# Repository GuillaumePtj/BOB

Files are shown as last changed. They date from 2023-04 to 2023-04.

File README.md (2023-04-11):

# BOB

This project is carried out by a for students group in second year at ENSEA.

### Principal objectives

This project main goal is to realize a 5-axis robot arm. This robot is a prototype concive to help people with disabilities. 

### Requirement

This project is realized in collaboration with a clinique, and some decision were taken.
The robot need :

  * to draw its power supply from the grid
  * to be able to pick up something from the floor where he stand
  * to be connected at the wheelchair of the patient in bluetooth
  * to be controled by the bluetooth and by a touch interface
  * to be fixed on a table 

Some decision where also taken for some technical reasons.
The robot :

  * contain a raspberry PI 4, and a STM32
  * present a total of 3 servomotors ans 3 steppers

---------------

# The realisation

### Mecanics

 The majority of the parts are modeled on SOLIDWORKS, and printed in 3D by the school. The mecanical parts (rollings, belt,...) are bought on RScomponents.  
Some other parts are given by the mechanical workshop.  
Files are available in the Meca branch.

-----
### Hardware

The hardware part is composed by 5 main devices :

 * The STM32
 * The Raspberry PI 4
 * The AC/DC converter
 * The power module
 * The driver module

All those devices are placed in the robot base and connected by cable to each other, and to other parts.  
The Raspberry is needed here because she offer wi-fi, bluetooth, serial connection, and good performances.  
STM32 is used because of his great ability to real time work, which is better for motor control.  
AC/DC converter take the 230V / 50Hz in input and comes out of 24V.  
The power module take the 24V, and divide it to provide 12V, 7.4V, 5V, and 3.3V.  
The driver module contain 4 driver for stepper.
All the PCB are designed on kiCad

Untitled Diagram drawio(2)

-----
### Software

The Python code has been written on VSCode, and C code has been written on STM32CubeIDE.
All the codes are available in Code branch.

### Raspberry code

The Raspberry has already been configurate by activating SSH protocole and Wi-Fi.

**code actually runing into the robot**  
The raspberry and the STM communicate in UART. The raspberry sends the positioning data destined for a single motor to the STM with one single data frame of 7 bytes.
In order we have:  
Start of frame, engine number, engine angle, direction of rotation, rotation Speed, end of frame.
 
**Drafted but needs to be implemented later**  
We take the base of the first code except that this time we seek to direct the motors with the coordinates according to the X, Y, Z positions of our reference.
The frame sent is the following this time made of :  
Start of frame, Position along X and around X, Position along Y and around Y, Position along Z and around Z, End of frame.

More information in the "matrix" section

### STM32 code

Step to receive and use the data frame by UART :
- UART port binary speed: 9600  in interrupt mode 
- In CallBack function : Set a flag then receive the data frame into an integer array
- In the main function : We split the data written in the array
- Send the data to the motors

The datas received are : motor number, wanted angle, direction and speed.
The wrist and the gripper are controlled with servo motors. Shoulder and elbow are controlled by stepper motors.
When the robot is initialized, the servomotors move to their "central" position and their LEDs are green. After a short time they turn purple and the robot is ready to receive instructions.

**Speed control :**

The stepper motors can be controlled with 3 different speeds which are managed by three differently set timers. For the servos we gave a value between 0 and 1023. The higher this number, the faster the motor will go. We have preset 3 different speeds for them too.

**Direction control :** 

For both types of motors, the direction is a bit of 0 or 1. The only difference between the two types of motors is that the servos cannot be rotated indefinitely. For each direction it has an angle of action of 150°, so 300° in total.

**Angle control :**

### Direction of the motors in the state of the pins

Motor 1 (Clamp) : 
 * 0->close
 * 1->open
 
Motor 2 (Wirst_Z) : 
 * 0->left
 * 1->right

Motor 3 (Wirst_X) : 
 * 0 -> down
 * 1 -> up

Motor 4 (Elbow) : 
 * 0 -> up
 * 1 -> down

-----
### Matrix system

Now that we are controlling the motors 1 by 1 by giving the angle command to each of the motors, it is time to control the motor in position. To put this into practice we have to go through a matrix system.  
The matrix system will allow us to find the angles that each motor must adopt for the robot to reach a desired position.

Ex :  
the Raspberry sends the following instructions to the STM:  
 * X Position
 * Y Position
 * Z Position
 * X orientation
 * Y orientation
 * Z orientation
 
 and with these instructions the robot should be able to get into the desired position.
 
It is necessary to establish the "direct geometric model" (this makes it possible to obtain the final position thanks to the angles of the given motors) and invert this model. In our case, we therefore use the "inverse geometric model" which makes it the opposite of the previous model: from a given position, the model calculates the angles for each motor and that is what we want.

What has already been done:

- The inverse geometry model has been established for the first 3 axes, the equations and the code have been written for the first 3 axes. All that's missing is to take into account the reduction ratios of each engine and add the factors in the code and then test the whole thing.

What remains to be done :

- Establish the inverse geometric model for the remaining 2 axes.

Good to know :

The inverse geometric model of the robot is done in two stages (position part and orientation part). The position part of the robot is done (part which manages the first 3 axes) and the orientation part (orientation of the gripper) which is managed by the remaining axes is to be done. For the resolution of the inverse geometry model of the last axes, it is necessary:

 1) establish the direct geometric model using the Denavit-Hartenberg method
 2) Inverse the model by using PAUL's method
 3) Once the equations of the remaining angles have been found, implement it in the STM
 
----------
### To go further

Some parts needs to be adapted, like the shoulder, the cable management, or the placement of the cards into the basement. 
The driver PCB doesn't work correctly, some debugging is needed.
The robot could be better with a last rotary axis, beetween the elbow and the wrist.  
The contrôle part as begun. But she is not implemented due to a bluetooth probleme and the fact that there is one articulation less.
The code in python need to work with interrupt so that we can use the Raspberry for interfacing while she send data frame.

----------
here is the datasheet of the [driver](https://www.trinamic.com/fileadmin/assets/Products/ICs_Documents/TMC2225_Datasheet_Rev1.11.pdf) for the steppers.  
here is the datasheet of the [servomotors](https://emanual.robotis.com/docs/en/dxl/x/xl320/).  
here is the documentation for the [STM32](https://www.st.com/resource/en/datasheet/stm32l412kb.pdf).

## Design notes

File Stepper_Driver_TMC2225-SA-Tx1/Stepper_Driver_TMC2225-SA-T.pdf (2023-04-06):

Page 1

# | Reference | Qty | Value | Footprint | DNP

1 | C1, C5, C6 | 3 10uF | Capacitor_SMD:CP_Elec_4x5.7
2 | C2, C3, C4, C7 | 4 100nF | Capacitor_SMD:C_0603_1608Metric_Pad1.08x0.95mm_HandSolder
3 C8 | | 1 22nF | Capacitor_SMD:C_0603_1608Metric_Pad1.08x0.95mm_HandSolder
4 | C9 | 1 2.2uF | Capacitor_SMD:C_0805_2012Metric_Pad1.18x1.45mm_HandSolder
5 | D1, D2 | 2 LED | LED_SMD:LED_0603_1608Metric_Pad1.05x0.95mm_HandSolder
6 H1, H2, H3, H4 | | 4 MountingHole_Pad | MountingHole:MountingHole_3.2mm_M3_Pad_Via
7 | J1 | 1 Conn_01x03_Male | Connector_JST:JST_XH_B3B-XH-A_1x03_P2.50mm_Vertical
8 J2 | | 1 Conn_01x07 | Connector_JST:JST_XH_B7B-XH-A_1x07_P2.50mm_Vertical
9 J3 | | 1 Conn_01x07 | Connector_PinHeader_2.54mm:PinHeader_1x07_P2.54mm_Vertical
10 | J4, J5, J6 | 3 Conn_01x05 | Connector_PinHeader_2.54mm:PinHeader_1x05_P2.54mm_Vertical
11 | J7 | 1 Conn_01x04_Female | Connector_JST:JST_XH_B4B-XH-A_1x04_P2.50mm_Vertical
12 | J8 | 1 Conn_01x05_Female | Connector_JST:JST_XH_B5B-XH-A_1x05_P2.50mm_Vertical
13 | R1 | 1 110m | Resistor_SMD:R_0603_1608Metric_Pad0.98x0.95mm_HandSolder
14 | R2, R7, R10 | 3 1k | Resistor_SMD:R_0603_1608Metric_Pad0.98x0.95mm_HandSolder
15 | R3, R4, R5, R6 | 4 0R | Resistor_SMD:R_0603_1608Metric_Pad0.98x0.95mm_HandSolder
16 | R8, R9 | 2 150m | Resistor_SMD:R_1206_3216Metric_Pad1.30x1.75mm_HandSolder
17 | U1 | 1 TMC2225-SA-T | Package_SO:HTSSOP-28-1EP_4.4x9.7mm_P0.65mm_EP2.85x5.4mm_ThermalVias

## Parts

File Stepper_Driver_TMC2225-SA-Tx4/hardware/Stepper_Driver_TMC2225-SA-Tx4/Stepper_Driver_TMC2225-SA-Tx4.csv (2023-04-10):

Source: | /home/gui/Downloads/Stepper_Driver_TMC2225-SA-Tx4/hardware/Stepper_Driver_TMC2225-SA-Tx4/Stepper_Driver_TMC2225-SA-Tx4.kicad_sch
Date: | mar. 28 mars 2023 13:58:16
Tool: | Eeschema 6.0.10-86aedd382b~118~ubuntu22.04.1
Generator: | /usr/share/kicad/plugins/bom_csv_grouped_by_value.py
Component Count: | 84
Individual Components:
Item | Qty | Reference(s) | Value | LibPart | Footprint | Datasheet
 |  | C1 | 1uF | Device:C | Capacitor_SMD:C_0603_1608Metric_Pad1.08x0.95mm_HandSolder | ~
 |  | C2 | 100nF | Device:C | Capacitor_SMD:C_0603_1608Metric_Pad1.08x0.95mm_HandSolder | ~
 |  | C3 | 100uF | Device:C_Polarized | Capacitor_SMD:CP_Elec_10x10.5 | ~
 |  | C4 | 1uF | Device:C | Capacitor_SMD:C_0603_1608Metric_Pad1.08x0.95mm_HandSolder | ~
 |  | C5 | 100nF | Device:C | Capacitor_SMD:C_0603_1608Metric_Pad1.08x0.95mm_HandSolder | ~
 |  | C6 | 100nF | Device:C | Capacitor_SMD:C_0603_1608Metric_Pad1.08x0.95mm_HandSolder | ~
 |  | C7 | 22nF | Device:C | Capacitor_SMD:C_0603_1608Metric_Pad1.08x0.95mm_HandSolder | ~
 |  | C8 | 10uF | Device:C_Polarized | Capacitor_SMD:CP_Elec_4x5.7 | ~
 |  | C9 | 100nF | Device:C | Capacitor_SMD:C_0603_1608Metric_Pad1.08x0.95mm_HandSolder | ~
 |  | C10 | 100nF | Device:C | Capacitor_SMD:C_0603_1608Metric_Pad1.08x0.95mm_HandSolder | ~
 |  | C11 | 100nF | Device:C | Capacitor_SMD:C_0603_1608Metric_Pad1.08x0.95mm_HandSolder | ~
 |  | C12 | 100uF | Device:C_Polarized | Capacitor_SMD:CP_Elec_6.3x7.7 | ~
 |  | C13 | 2.2uF | Device:C | Capacitor_SMD:C_0603_1608Metric_Pad1.08x0.95mm_HandSolder | ~
 |  | C14 | 100nF | Device:C | Capacitor_SMD:C_0603_1608Metric_Pad1.08x0.95mm_HandSolder | ~
 |  | C15 | 22nF | Device:C | Capacitor_SMD:C_0603_1608Metric_Pad1.08x0.95mm_HandSolder | ~
 |  | C16 | 10uF | Device:C_Polarized | Capacitor_SMD:CP_Elec_4x5.7 | ~
 |  | C17 | 100nF | Device:C | Capacitor_SMD:C_0603_1608Metric_Pad1.08x0.95mm_HandSolder | ~
 |  | C18 | 100nF | Device:C | Capacitor_SMD:C_0603_1608Metric_Pad1.08x0.95mm_HandSolder | ~
 |  | C19 | 100nF | Device:C | Capacitor_SMD:C_0603_1608Metric_Pad1.08x0.95mm_HandSolder | ~
 |  | C20 | 100uF | Device:C_Polarized | Capacitor_SMD:CP_Elec_6.3x7.7 | ~
 |  | C21 | 2.2uF | Device:C | Capacitor_SMD:C_0603_1608Metric_Pad1.08x0.95mm_HandSolder | ~
 |  | C22 | 100nF | Device:C | Capacitor_SMD:C_0603_1608Metric_Pad1.08x0.95mm_HandSolder | ~
 |  | C23 | 22nF | Device:C | Capacitor_SMD:C_0603_1608Metric_Pad1.08x0.95mm_HandSolder | ~
 |  | C24 | 10uF | Device:C_Polarized | Capacitor_SMD:CP_Elec_4x5.7 | ~
 |  | C25 | 100nF | Device:C | Capacitor_SMD:C_0603_1608Metric_Pad1.08x0.95mm_HandSolder | ~
 |  | C26 | 100nF | Device:C | Capacitor_SMD:C_0603_1608Metric_Pad1.08x0.95mm_HandSolder | ~
 |  | C27 | 100nF | Device:C | Capacitor_SMD:C_0603_1608Metric_Pad1.08x0.95mm_HandSolder | ~
 |  | C28 | 100uF | Device:C_Polarized | Capacitor_SMD:CP_Elec_6.3x7.7 | ~
 |  | C29 | 2.2uF | Device:C | Capacitor_SMD:C_0603_1608Metric_Pad1.08x0.95mm_HandSolder | ~
 |  | C30 | 100nF | Device:C | Capacitor_SMD:C_0603_1608Metric_Pad1.08x0.95mm_HandSolder | ~
 |  | C31 | 22nF | Device:C | Capacitor_SMD:C_0603_1608Metric_Pad1.08x0.95mm_HandSolder | ~
 |  | C32 | 10uF | Device:C_Polarized | Capacitor_SMD:CP_Elec_4x5.7 | ~
 |  | C33 | 100nF | Device:C | Capacitor_SMD:C_0603_1608Metric_Pad1.08x0.95mm_HandSolder | ~
 |  | C34 | 100nF | Device:C | Capacitor_SMD:C_0603_1608Metric_Pad1.08x0.95mm_HandSolder | ~
 |  | C35 | 100nF | Device:C | Capacitor_SMD:C_0603_1608Metric_Pad1.08x0.95mm_HandSolder | ~
 |  | C36 | 100uF | Device:C_Polarized | Capacitor_SMD:CP_Elec_6.3x7.7 | ~
 |  | C37 | 2.2uF | Device:C | Capacitor_SMD:C_0603_1608Metric_Pad1.08x0.95mm_HandSolder | ~
 |  | D1 | LED | Device:LED | LED_SMD:LED_0603_1608Metric_Pad1.05x0.95mm_HandSolder | ~
 |  | D2 | LED | Device:LED | LED_SMD:LED_0603_1608Metric_Pad1.05x0.95mm_HandSolder | ~
 |  | D3 | LED | Device:LED | LED_SMD:LED_0603_1608Metric_Pad1.05x0.95mm_HandSolder | ~
 |  | D4 | LED | Device:LED | LED_SMD:LED_0603_1608Metric_Pad1.05x0.95mm_HandSolder | ~
 |  | D5 | LED | Device:LED | LED_SMD:LED_0603_1608Metric_Pad1.05x0.95mm_HandSolder | ~
 |  | D6 | LED | Device:LED | LED_SMD:LED_0603_1608Metric_Pad1.05x0.95mm_HandSolder | ~
 |  | H1 | MountingHole_Pad | Mechanical:MountingHole_Pad | MountingHole:MountingHole_3.2mm_M3_Pad_Via | ~
 |  | H2 | MountingHole_Pad | Mechanical:MountingHole_Pad | MountingHole:MountingHole_3.2mm_M3_Pad_Via | ~
 |  | H3 | MountingHole_Pad | Mechanical:MountingHole_Pad | MountingHole:MountingHole_3.2mm_M3_Pad_Via | ~
 |  | H4 | MountingHole_Pad | Mechanical:MountingHole_Pad | MountingHole:MountingHole_3.2mm_M3_Pad_Via | ~
 |  | J1 | Conn_01x05 | Connector_Generic:Conn_01x05 | Connector_JST:JST_XH_B5B-XH-A_1x05_P2.50mm_Vertical | ~
 |  | J2 | Conn_01x05 | Connector_Generic:Conn_01x05 | Connector_JST:JST_XH_B5B-XH-A_1x05_P2.50mm_Vertical | ~
 |  | J3 | Conn_01x03_Male | Connector:Conn_01x03_Male | Connector_JST:JST_XH_B3B-XH-A_1x03_P2.50mm_Vertical | ~
 |  | J4 | Conn_01x04_Female | Connector:Conn_01x04_Female | Connector_JST:JST_XH_B4B-XH-A_1x04_P2.50mm_Vertical | ~
 |  | J5 | Conn_01x04_Female | Connector:Conn_01x04_Female | Connector_JST:JST_XH_B4B-XH-A_1x04_P2.50mm_Vertical | ~
 |  | J6 | Conn_01x04_Female | Connector:Conn_01x04_Female | Connector_JST:JST_XH_B4B-XH-A_1x04_P2.50mm_Vertical | ~
 |  | J7 | Conn_01x04_Female | Connector:Conn_01x04_Female | Connector_JST:JST_XH_B4B-XH-A_1x04_P2.50mm_Vertical | ~
 |  | JP1 | SolderJumper_3_Bridged12 | Jumper:SolderJumper_3_Bridged12 | Jumper:SolderJumper-3_P1.3mm_Bridged12_RoundedPad1.0x1.5mm_NumberLabels | ~
 |  | JP2 | SolderJumper_3_Bridged12 | Jumper:SolderJumper_3_Bridged12 | Jumper:SolderJumper-3_P1.3mm_Bridged12_RoundedPad1.0x1.5mm_NumberLabels | ~
 |  | JP3 | SolderJumper_3_Bridged12 | Jumper:SolderJumper_3_Bridged12 | Jumper:SolderJumper-3_P1.3mm_Bridged12_RoundedPad1.0x1.5mm_NumberLabels | ~
 |  | JP4 | SolderJumper_3_Bridged12 | Jumper:SolderJumper_3_Bridged12 | Jumper:SolderJumper-3_P1.3mm_Bridged12_RoundedPad1.0x1.5mm_NumberLabels | ~
 |  | JP5 | SolderJumper_3_Bridged12 | Jumper:SolderJumper_3_Bridged12 | Jumper:SolderJumper-3_P1.3mm_Bridged12_RoundedPad1.0x1.5mm_NumberLabels | ~
 |  | JP6 | SolderJumper_3_Bridged12 | Jumper:SolderJumper_3_Bridged12 | Jumper:SolderJumper-3_P1.3mm_Bridged12_RoundedPad1.0x1.5mm_NumberLabels | ~
 |  | JP7 | SolderJumper_3_Bridged12 | Jumper:SolderJumper_3_Bridged12 | Jumper:SolderJumper-3_P1.3mm_Bridged12_RoundedPad1.0x1.5mm_NumberLabels | ~
 |  | JP8 | SolderJumper_3_Bridged12 | Jumper:SolderJumper_3_Bridged12 | Jumper:SolderJumper-3_P1.3mm_Bridged12_RoundedPad1.0x1.5mm_NumberLabels | ~
 |  | R1 | 1k | Device:R | Resistor_SMD:R_0603_1608Metric_Pad0.98x0.95mm_HandSolder | ~
 |  | R2 | 1k | Device:R | Resistor_SMD:R_0603_1608Metric_Pad0.98x0.95mm_HandSolder | ~
 |  | R3 | 110m | Device:R | Resistor_SMD:R_1206_3216Metric_Pad1.30x1.75mm_HandSolder | ~
 |  | R4 | 150m | Device:R | Resistor_SMD:R_1206_3216Metric_Pad1.30x1.75mm_HandSolder | ~
 |  | R5 | 150m | Device:R | Resistor_SMD:R_1206_3216Metric_Pad1.30x1.75mm_HandSolder | ~
 |  | R6 | 1k | Device:R | Resistor_SMD:R_0603_1608Metric_Pad0.98x0.95mm_HandSolder | ~
 |  | R7 | 110m | Device:R | Resistor_SMD:R_1206_3216Metric_Pad1.30x1.75mm_HandSolder | ~
 |  | R8 | 150m | Device:R | Resistor_SMD:R_1206_3216Metric_Pad1.30x1.75mm_HandSolder | ~
 |  | R9 | 150m | Device:R | Resistor_SMD:R_1206_3216Metric_Pad1.30x1.75mm_HandSolder | ~
 |  | R10 | 1k | Device:R | Resistor_SMD:R_0603_1608Metric_Pad0.98x0.95mm_HandSolder | ~
 |  | R11 | 110m | Device:R | Resistor_SMD:R_1206_3216Metric_Pad1.30x1.75mm_HandSolder | ~
 |  | R12 | 150m | Device:R | Resistor_SMD:R_1206_3216Metric_Pad1.30x1.75mm_HandSolder | ~
 |  | R13 | 150m | Device:R | Resistor_SMD:R_1206_3216Metric_Pad1.30x1.75mm_HandSolder | ~
 |  | R14 | 1k | Device:R | Resistor_SMD:R_0603_1608Metric_Pad0.98x0.95mm_HandSolder | ~
 |  | R15 | 110m | Device:R | Resistor_SMD:R_1206_3216Metric_Pad1.30x1.75mm_HandSolder | ~
 |  | R16 | 150m | Device:R | Resistor_SMD:R_1206_3216Metric_Pad1.30x1.75mm_HandSolder | ~
 |  | R17 | 150m | Device:R | Resistor_SMD:R_1206_3216Metric_Pad1.30x1.75mm_HandSolder | ~
 |  | R18 | 1k | Device:R | Resistor_SMD:R_0603_1608Metric_Pad0.98x0.95mm_HandSolder | ~
 |  | U1 | TMC2225-SA-T | Custom_laptop:TMC2225-SA-T | Package_SO:HTSSOP-28-1EP_4.4x9.7mm_P0.65mm_EP2.85x5.4mm_ThermalVias
 |  | U2 | TMC2225-SA-T | Custom_laptop:TMC2225-SA-T | Package_SO:HTSSOP-28-1EP_4.4x9.7mm_P0.65mm_EP2.85x5.4mm_ThermalVias
 |  | U3 | TMC2225-SA-T | Custom_laptop:TMC2225-SA-T | Package_SO:HTSSOP-28-1EP_4.4x9.7mm_P0.65mm_EP2.85x5.4mm_ThermalVias
 |  | U4 | TMC2225-SA-T | Custom_laptop:TMC2225-SA-T | Package_SO:HTSSOP-28-1EP_4.4x9.7mm_P0.65mm_EP2.85x5.4mm_ThermalVias
Collated Components:
Item | Qty | Reference(s) | Value | LibPart | Footprint | Datasheet
1 | 2 | C1, C4 | 1uF | Device:C | Capacitor_SMD:C_0603_1608Metric_Pad1.08x0.95mm_HandSolder | ~
2 | 18 | C2, C5, C6, C9, C10, C11, C14, C17, C18, C19, C22, C25, C26, C27, C30, C33, C34, C35 | 100nF | Device:C | Capacitor_SMD:C_0603_1608Metric_Pad1.08x0.95mm_HandSolder | ~
3 | 1 | C3 | 100uF | Device:C_Polarized | Capacitor_SMD:CP_Elec_10x10.5 | ~
4 | 4 | C7, C15, C23, C31 | 22nF | Device:C | Capacitor_SMD:C_0603_1608Metric_Pad1.08x0.95mm_HandSolder | ~
5 | 4 | C8, C16, C24, C32 | 10uF | Device:C_Polarized | Capacitor_SMD:CP_Elec_4x5.7 | ~
6 | 4 | C12, C20, C28, C36 | 100uF | Device:C_Polarized | Capacitor_SMD:CP_Elec_6.3x7.7 | ~
7 | 4 | C13, C21, C29, C37 | 2.2uF | Device:C | Capacitor_SMD:C_0603_1608Metric_Pad1.08x0.95mm_HandSolder | ~
8 | 6 | D1, D2, D3, D4, D5, D6 | LED | Device:LED | LED_SMD:LED_0603_1608Metric_Pad1.05x0.95mm_HandSolder | ~
9 | 4 | H1, H2, H3, H4 | MountingHole_Pad | Mechanical:MountingHole_Pad | MountingHole:MountingHole_3.2mm_M3_Pad_Via | ~
10 | 2 | J1, J2 | Conn_01x05 | Connector_Generic:Conn_01x05 | Connector_JST:JST_XH_B5B-XH-A_1x05_P2.50mm_Vertical | ~
11 | 1 | J3 | Conn_01x03_Male | Connector:Conn_01x03_Male | Connector_JST:JST_XH_B3B-XH-A_1x03_P2.50mm_Vertical | ~
12 | 4 | J4, J5, J6, J7 | Conn_01x04_Female | Connector:Conn_01x04_Female | Connector_JST:JST_XH_B4B-XH-A_1x04_P2.50mm_Vertical | ~
13 | 8 | JP1, JP2, JP3, JP4, JP5, JP6, JP7, JP8 | SolderJumper_3_Bridged12 | Jumper:SolderJumper_3_Bridged12 | Jumper:SolderJumper-3_P1.3mm_Bridged12_RoundedPad1.0x1.5mm_NumberLabels | ~
14 | 6 | R1, R2, R6, R10, R14, R18 | 1k | Device:R | Resistor_SMD:R_0603_1608Metric_Pad0.98x0.95mm_HandSolder | ~
15 | 4 | R3, R7, R11, R15 | 110m | Device:R | Resistor_SMD:R_1206_3216Metric_Pad1.30x1.75mm_HandSolder | ~
16 | 8 | R4, R5, R8, R9, R12, R13, R16, R17 | 150m | Device:R | Resistor_SMD:R_1206_3216Metric_Pad1.30x1.75mm_HandSolder | ~
17 | 4 | U1, U2, U3, U4 | TMC2225-SA-T | Custom_laptop:TMC2225-SA-T | Package_SO:HTSSOP-28-1EP_4.4x9.7mm_P0.65mm_EP2.85x5.4mm_ThermalVias

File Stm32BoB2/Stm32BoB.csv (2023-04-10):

Source: | Y:\Ensea\2A\KiCad\Stm32BoB2\Stm32BoB.kicad_sch
Date: | 04/04/2023 18:03:43
Tool: | Eeschema 7.0.1
Generator: | Y:\Ensea\2A\KiCad\7.0\bin\scripting\plugins/bom_csv_grouped_by_value_with_fp.py
Component Count: | 33
Ref | Qnty | Value | Cmp name | Footprint | Description | Vendor | DNP
C1, C2 | 2 | 10u | C | Capacitor_SMD:C_0603_1608Metric_Pad1.08x0.95mm_HandSolder | Unpolarized capacitor
C3, C5, C6, C7 | 4 | 100n | C | Capacitor_SMD:C_0603_1608Metric_Pad1.08x0.95mm_HandSolder | Unpolarized capacitor
C4 | 1 | 4.7u | C | Capacitor_SMD:C_0603_1608Metric_Pad1.08x0.95mm_HandSolder | Unpolarized capacitor
D1 | 1 | LED_RED | LED | LED_SMD:LED_0603_1608Metric_Pad1.05x0.95mm_HandSolder | Light emitting diode
D2 | 1 | LED | LED | LED_SMD:LED_0603_1608Metric_Pad1.05x0.95mm_HandSolder | Light emitting diode
H1, H2, H3, H4 | 4 | MountingHole_Pad | MountingHole_Pad | MountingHole:MountingHole_2.7mm_Pad_Via | Mounting Hole with connection
J1 | 1 | Shield_RaspPi | Conn_01x05 | Connector_PinSocket_2.54mm:PinSocket_1x05_P2.54mm_Vertical | Generic connector, single row, 01x05, script generated (kicad-library-utils/schlib/autogen/connector/)
J2, J3, J4, J7, J8 | 5 | Conn_01x02 | Conn_01x02 | Connector_JST:JST_XH_B2B-XH-A_1x02_P2.50mm_Vertical | Generic connector, single row, 01x02, script generated (kicad-library-utils/schlib/autogen/connector/)
J5 | 1 | Servo_Com | Conn_01x03 | Connector_JST:JST_XH_B3B-XH-A_1x03_P2.50mm_Vertical | Generic connector, single row, 01x03, script generated (kicad-library-utils/schlib/autogen/connector/)
J6 | 1 | Conn_02x20_Odd_Even | Conn_02x20_Odd_Even | Connector_PinHeader_2.54mm:PinHeader_2x20_P2.54mm_Vertical | Generic connector, double row, 02x20, odd/even pin numbering scheme (row 1 odd numbers, row 2 even numbers), script generated (kicad-library-utils/schlib/autogen/connector/)
J9 | 1 | Conn_ST_STDC14 | Conn_ST_STDC14 | Connector_PinHeader_1.27mm:PinHeader_2x07_P1.27mm_Vertical_SMD | ST Debug Connector, standard ARM Cortex-M SWD and JTAG interface plus UART
J10, J11 | 2 | Conn_01x05 | Conn_01x05 | Connector_JST:JST_XH_B5B-XH-A_1x05_P2.50mm_Vertical | Generic connector, single row, 01x05, script generated (kicad-library-utils/schlib/autogen/connector/)
R1, R3 | 2 | 1k | R | Resistor_SMD:R_0603_1608Metric_Pad0.98x0.95mm_HandSolder | Resistor
R2 | 1 | 100k | R_Small | Resistor_SMD:R_0603_1608Metric_Pad0.98x0.95mm_HandSolder | Resistor, small symbol
R4, R5, R6 | 3 | 10k | R | Resistor_SMD:R_0603_1608Metric_Pad0.98x0.95mm_HandSolder | Resistor
SW1 | 1 | SW_Push | SW_Push | Button_Switch_SMD:SW_SPST_B3U-1000P | Push button switch, generic, two pins
U1 | 1 | AMS1117-3.3 | AMS1117-3.3 | Package_TO_SOT_SMD:SOT-223-3_TabPin2 | 1A Low Dropout regulator, positive, 3.3V fixed output, SOT-223
U2 | 1 | STM32L412KBT6 | STM32L412KBTx | Package_QFP:LQFP-32_7x7mm_P0.8mm | STMicroelectronics Arm Cortex-M4 MCU, 128KB flash, 40KB RAM, 80 MHz, 1.71-3.6V, 26 GPIO, LQFP32

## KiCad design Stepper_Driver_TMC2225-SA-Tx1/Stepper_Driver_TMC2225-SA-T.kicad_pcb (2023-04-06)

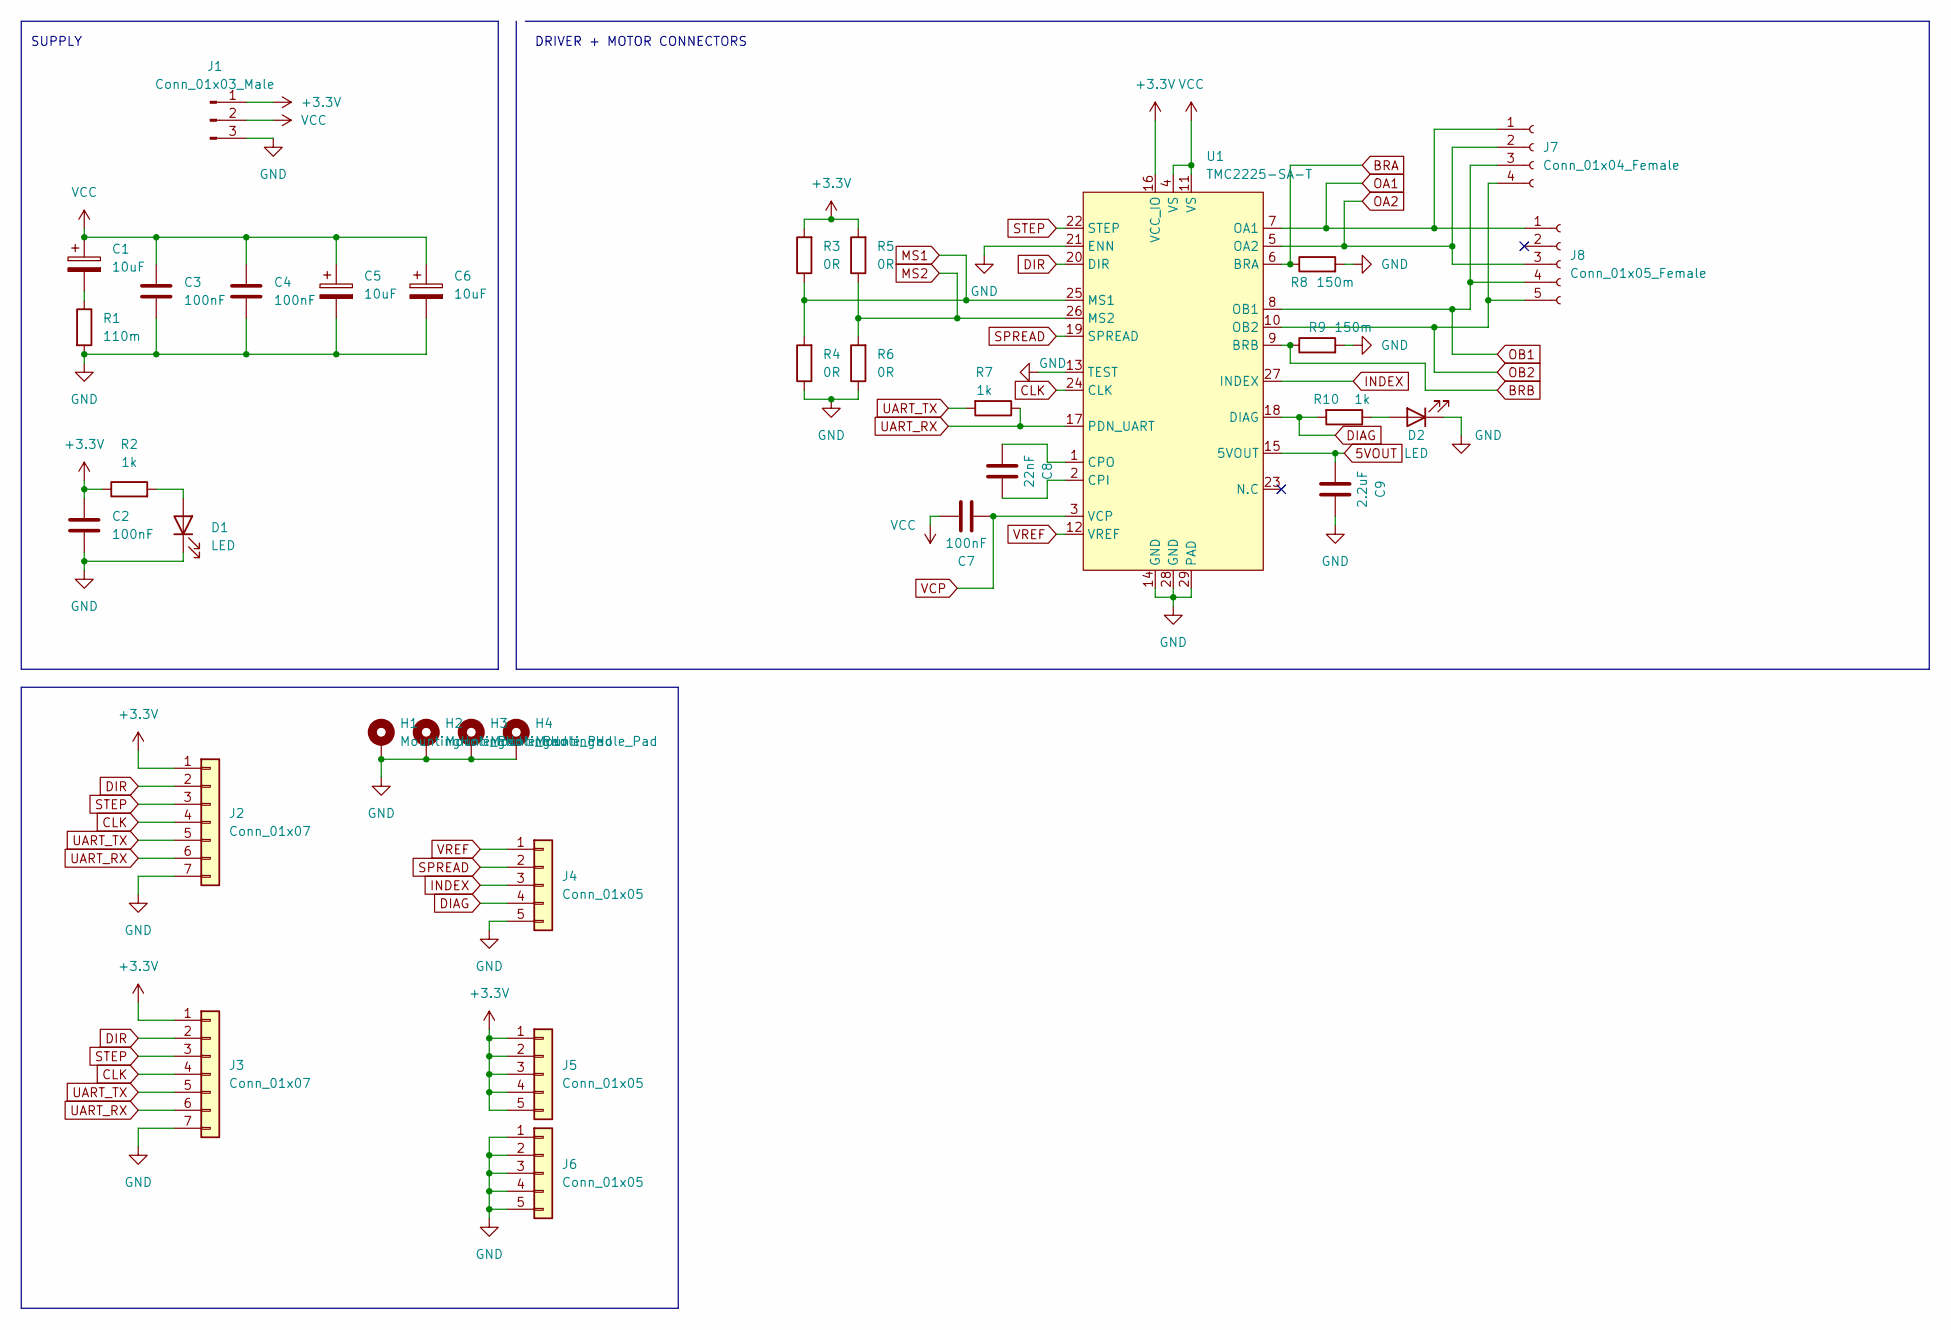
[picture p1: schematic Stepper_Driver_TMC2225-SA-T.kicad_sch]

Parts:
C1, C5, C6: 10uF; CP_Elec_4x5.7
C2, C3, C4, C7: 100nF; C_0603_1608Metric_Pad1.08x0.95mm_HandSolder
C8: 22nF; C_0603_1608Metric_Pad1.08x0.95mm_HandSolder
C9: 2.2uF; C_0805_2012Metric_Pad1.18x1.45mm_HandSolder
D1, D2: LED; LED_0603_1608Metric_Pad1.05x0.95mm_HandSolder
H1, H2, H3, H4: MountingHole_Pad; MountingHole_3.2mm_M3_Pad_Via
J1: Conn_01x03_Male; JST_XH_B3B-XH-A_1x03_P2.50mm_Vertical
J2: Conn_01x07; JST_XH_B7B-XH-A_1x07_P2.50mm_Vertical
J3: Conn_01x07; PinHeader_1x07_P2.54mm_Vertical
J4, J5, J6: Conn_01x05; PinHeader_1x05_P2.54mm_Vertical
J7: Conn_01x04_Female; JST_XH_B4B-XH-A_1x04_P2.50mm_Vertical
J8: Conn_01x05_Female; JST_XH_B5B-XH-A_1x05_P2.50mm_Vertical
R1: 110m; R_0603_1608Metric_Pad0.98x0.95mm_HandSolder
R2, R7, R10: 1k; R_0603_1608Metric_Pad0.98x0.95mm_HandSolder
R3, R4, R5, R6: 0R; R_0603_1608Metric_Pad0.98x0.95mm_HandSolder
R8, R9: 150m; R_1206_3216Metric_Pad1.30x1.75mm_HandSolder
U1: TMC2225-SA-T; HTSSOP-28-1EP_4.4x9.7mm_P0.65mm_EP2.85x5.4mm_ThermalVias

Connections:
5VOUT: C9.2, U1.15 (5VOUT)
+3.3V: C2.1, J1.1, J2.1, J3.1, J5.1, J5.2, J5.3, J5.4, J5.5, R2.1, R3.2, R5.2, U1.16 (VCC_IO)
BRA: R8.1, U1.6 (BRA)
BRB: R9.1, U1.9 (BRB)
CLK: J2.4, J3.4, U1.24 (CLK)
DIAG: J4.4, R10.2, U1.18 (DIAG)
DIR: J2.2, J3.2, U1.20 (DIR)
GND: C2.2, C3.2, C4.2, C5.2, C6.2, C9.1, D1.1 (K), D2.1 (K), H1.1, H2.1, H3.1, H4.1, J1.3, J2.7, J3.7, J4.5, J6.1, J6.2, J6.3, J6.4, J6.5, R1.2, R4.1, R6.1, R8.2, R9.2, U1.13 (TEST), U1.14 (GND), U1.21 (ENN), U1.28 (GND), U1.29 (PAD)
INDEX: J4.3, U1.27 (INDEX)
MS1: R3.1, R4.2, U1.25 (MS1)
MS2: R5.1, R6.2, U1.26 (MS2)
unnamed: C1.2, R1.1
unnamed: C8.1, U1.2 (CPI)
unnamed: C8.2, U1.1 (CPO)
unnamed: D1.2 (A), R2.2
unnamed: D2.2 (A), R10.1
OA1: J7.1, J8.1, U1.7 (OA1)
OA2: J7.2, J8.3, U1.5 (OA2)
OB1: J7.3, J8.4, U1.8 (OB1)
OB2: J7.4, J8.5, U1.10 (OB2)
SPREAD: J4.2, U1.19 (SPREAD)
STEP: J2.3, J3.3, U1.22 (STEP)
UART_RX: J2.6, J3.6, R7.1, U1.17 (PDN_UART)
UART_TX: J2.5, J3.5, R7.2
VCC: C1.1, C3.1, C4.1, C5.1, C6.1, C7.1, J1.2, U1.4 (VS), U1.11 (VS)
VCP: C7.2, U1.3 (VCP)
VREF: J4.1, U1.12 (VREF)

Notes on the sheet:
SUPPLY
DRIVER + MOTOR CONNECTORS

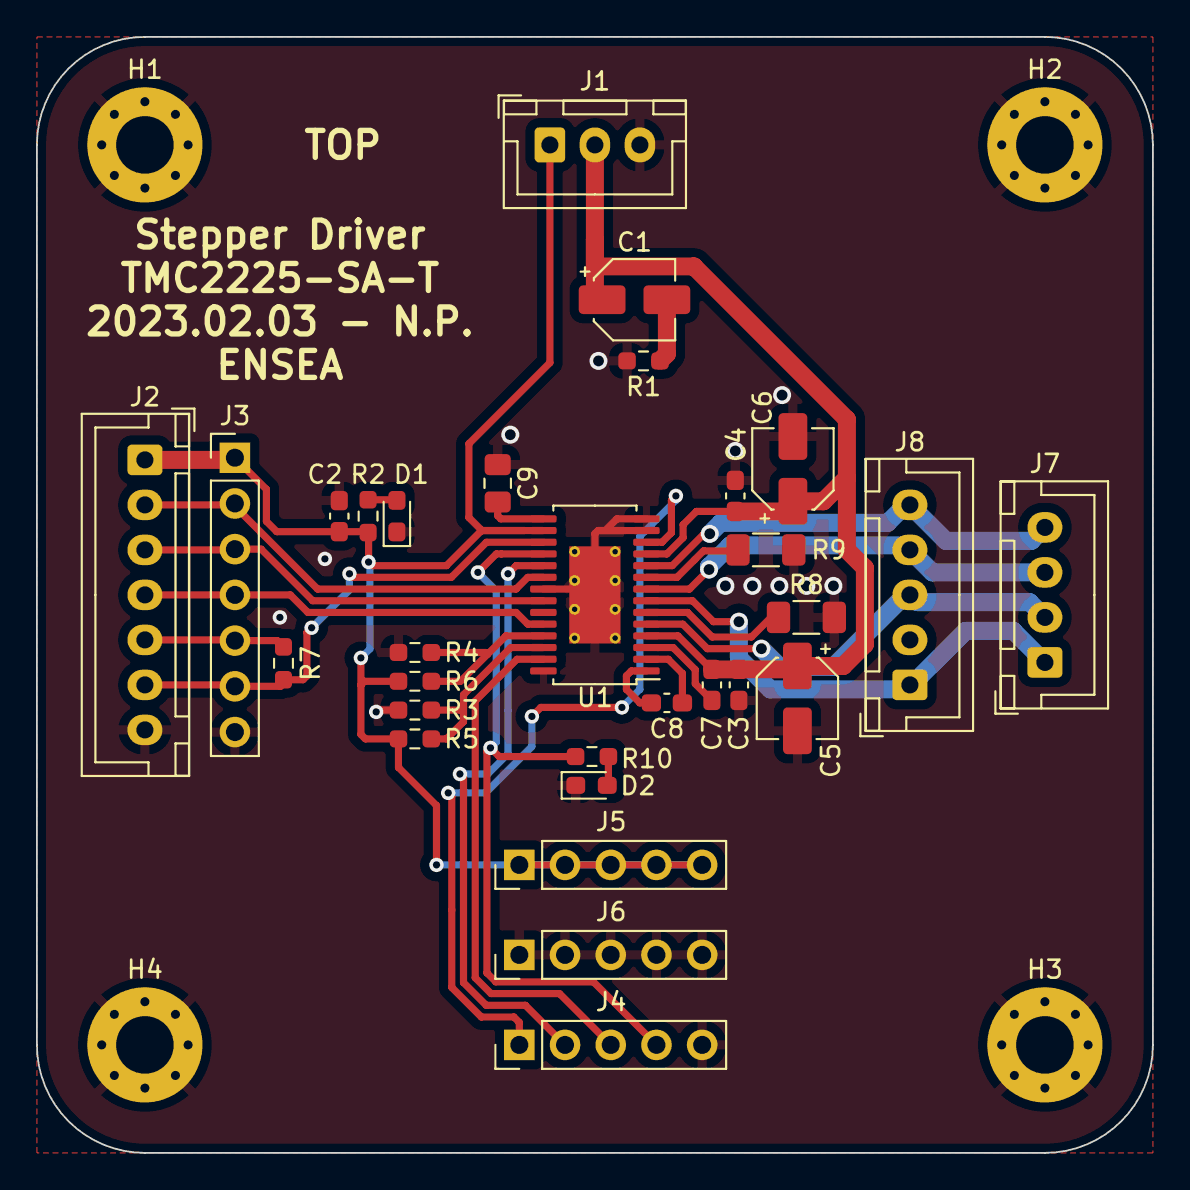
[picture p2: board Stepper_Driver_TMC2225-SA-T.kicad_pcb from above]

Board: 2 copper layers, 62.0 x 62.0 mm, 34 parts (0 on the bottom side), 27 nets.

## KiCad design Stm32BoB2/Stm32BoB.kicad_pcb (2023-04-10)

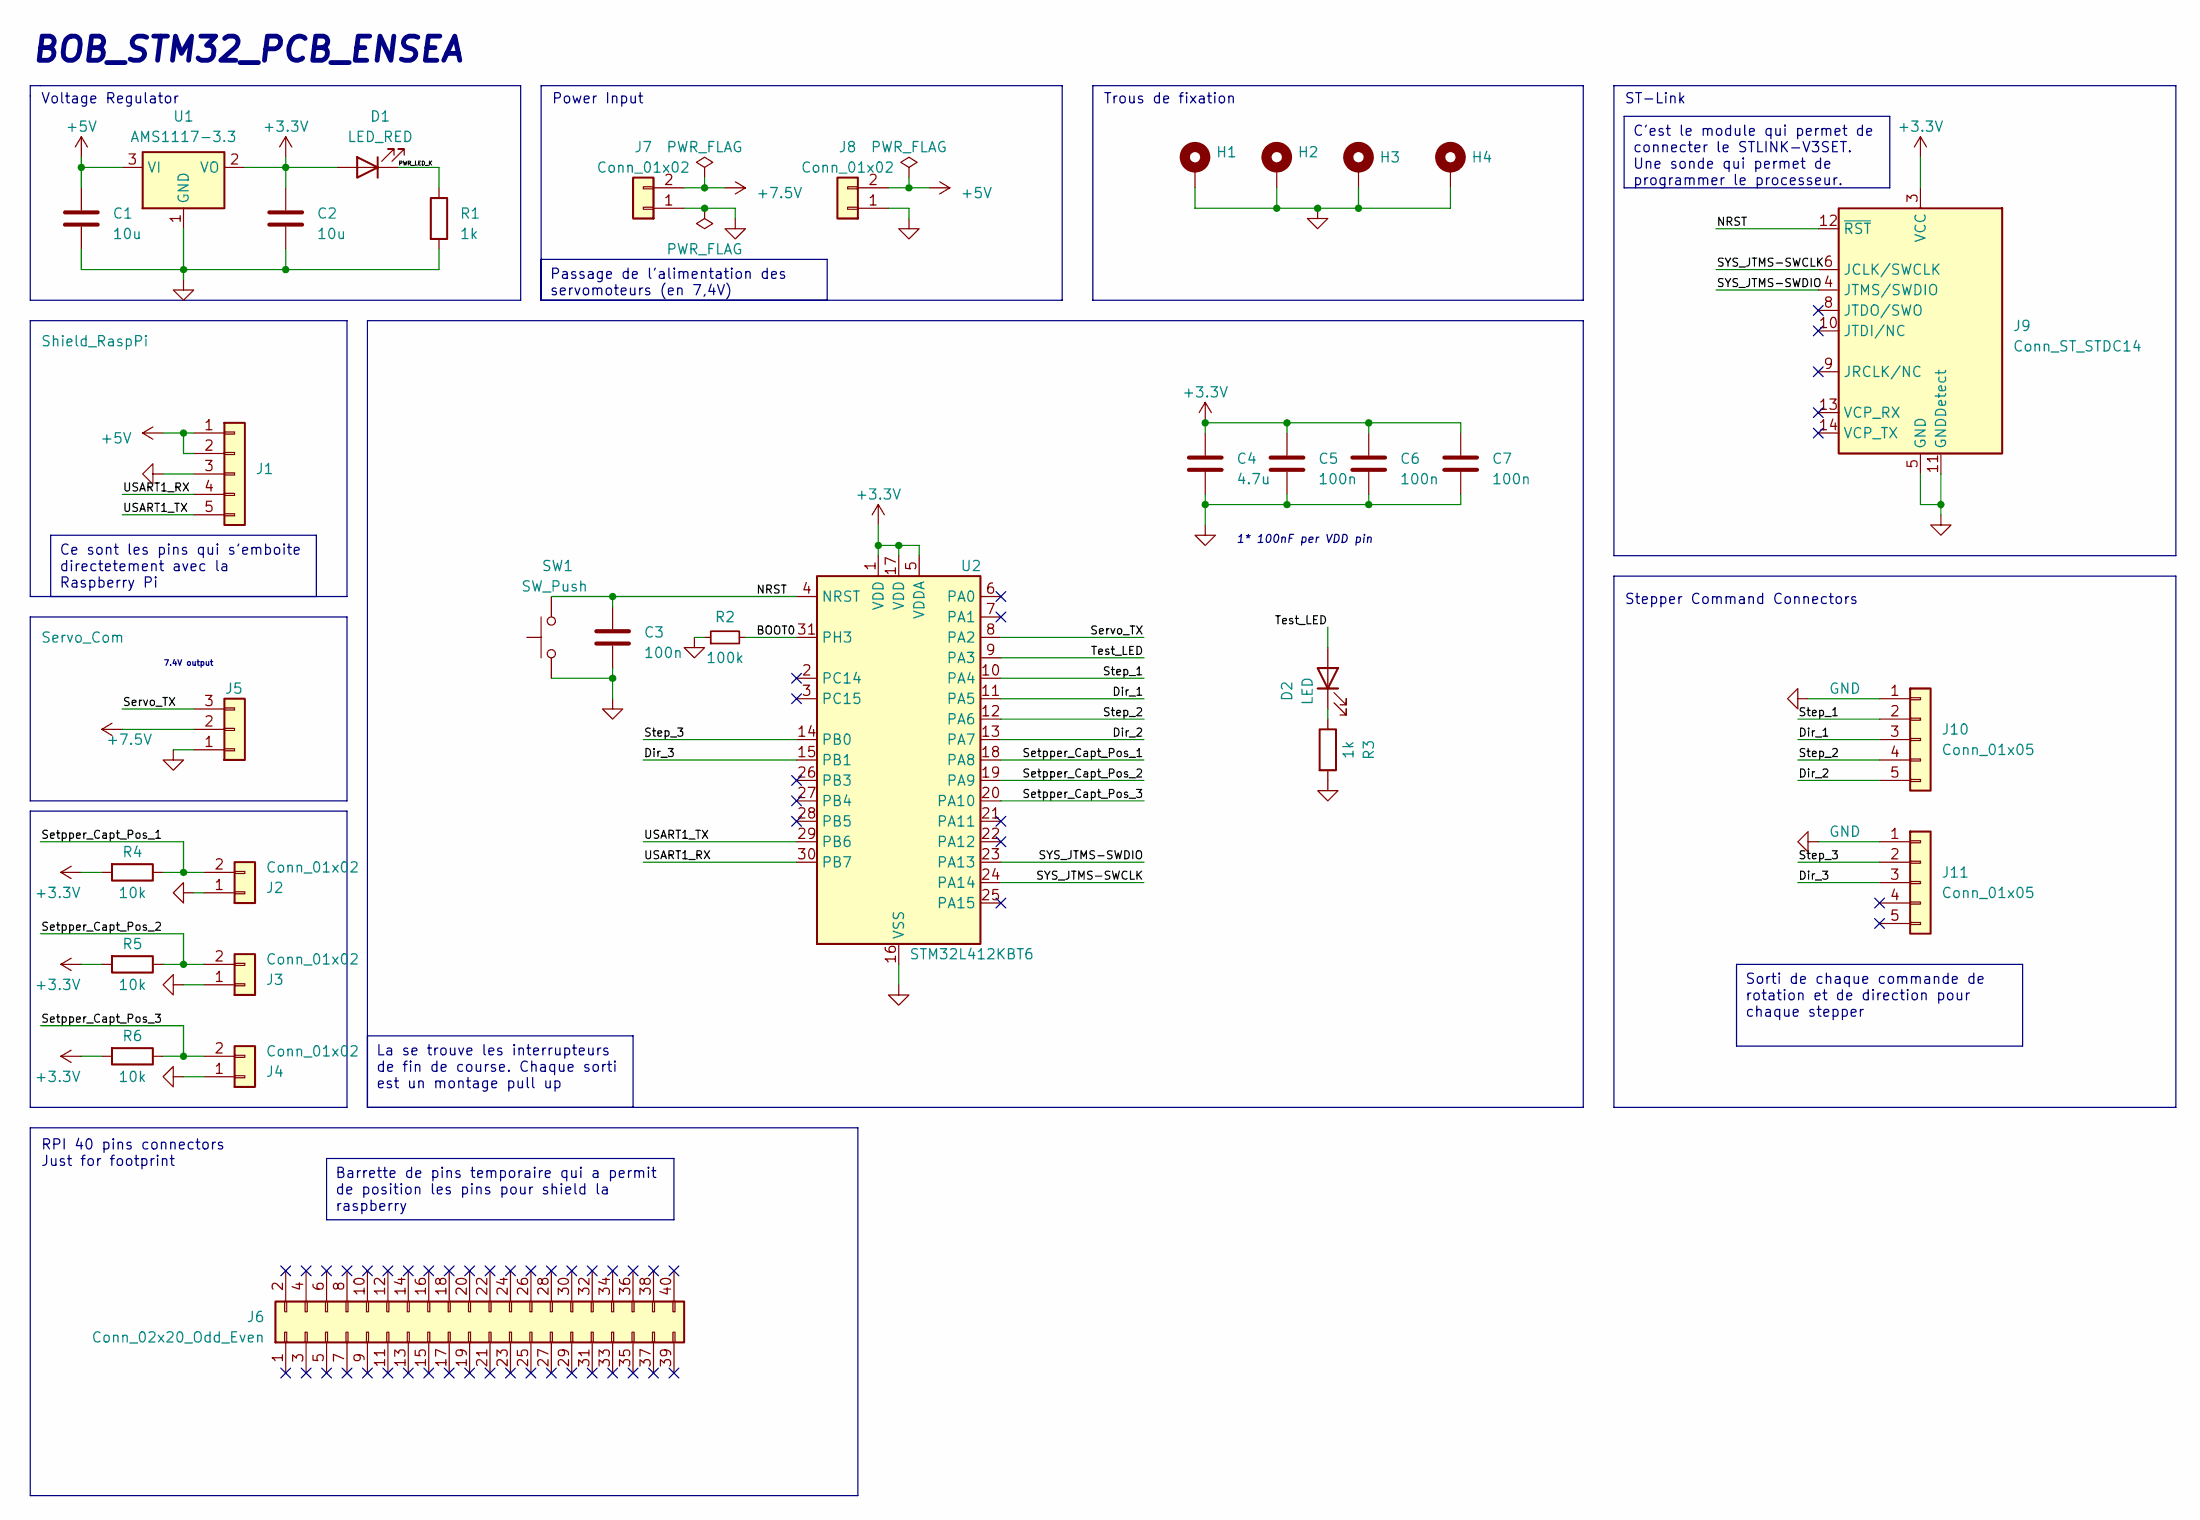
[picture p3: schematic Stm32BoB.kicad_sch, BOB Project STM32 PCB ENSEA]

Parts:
C1, C2: 10u; C_0603_1608Metric_Pad1.08x0.95mm_HandSolder
C3, C5, C6, C7: 100n; C_0603_1608Metric_Pad1.08x0.95mm_HandSolder
C4: 4.7u; C_0603_1608Metric_Pad1.08x0.95mm_HandSolder
D1: LED_RED; LED_0603_1608Metric_Pad1.05x0.95mm_HandSolder
D2: LED; LED_0603_1608Metric_Pad1.05x0.95mm_HandSolder
H1, H2, H3, H4: MountingHole_Pad; MountingHole_2.7mm_Pad_Via
J1: Shield_RaspPi; PinSocket_1x05_P2.54mm_Vertical
J2, J3, J4, J7, J8: Conn_01x02; JST_XH_B2B-XH-A_1x02_P2.50mm_Vertical
J5: Servo_Com; JST_XH_B3B-XH-A_1x03_P2.50mm_Vertical
J6: Conn_02x20_Odd_Even; PinHeader_2x20_P2.54mm_Vertical
J9: Conn_ST_STDC14; PinHeader_2x07_P1.27mm_Vertical_SMD
J10, J11: Conn_01x05; JST_XH_B5B-XH-A_1x05_P2.50mm_Vertical
R1, R3: 1k; R_0603_1608Metric_Pad0.98x0.95mm_HandSolder
R2: 100k; R_0603_1608Metric_Pad0.98x0.95mm_HandSolder
R4, R5, R6: 10k; R_0603_1608Metric_Pad0.98x0.95mm_HandSolder
SW1: SW_Push; SW_SPST_B3U-1000P
U1: AMS1117-3.3; SOT-223-3_TabPin2
U2: STM32L412KBT6; LQFP-32_7x7mm_P0.8mm

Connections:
+3.3V: C2.1, C4.1, C5.1, C6.1, C7.1, D1.2 (A), J9.3 (VCC), R4.2, R5.2, R6.2, U1.2 (VO), U2.1 (VDD), U2.5 (VDDA), U2.17 (VDD)
+5V: C1.1, J1.1, J1.2, J8.2, U1.3 (VI)
+7.5V: J5.2, J7.2
/BOOT0: R2.2, U2.31 (PH3)
/Dir_1: J10.3, U2.11 (PA5)
/Dir_2: J10.5, U2.13 (PA7)
/Dir_3: J11.3, U2.15 (PB1)
/NRST: C3.2, J9.12 (~RST), SW1.2, U2.4 (NRST)
/PWR_LED_K: D1.1 (K), R1.1
/SYS_JTMS-SWCLK: J9.6 (JCLK/SWCLK), U2.24 (PA14)
/SYS_JTMS-SWDIO: J9.4 (JTMS/SWDIO), U2.23 (PA13)
/Servo_TX: J5.3, U2.8 (PA2)
/Setpper_Capt_Pos_1: J2.2, R4.1, U2.18 (PA8)
/Setpper_Capt_Pos_2: J3.2, R5.1, U2.19 (PA9)
/Setpper_Capt_Pos_3: J4.2, R6.1, U2.20 (PA10)
/Step_1: J10.2, U2.10 (PA4)
/Step_2: J10.4, U2.12 (PA6)
/Step_3: J11.2, U2.14 (PB0)
/Test_LED: D2.2 (A), U2.9 (PA3)
/USART1_RX: J1.4, U2.30 (PB7)
/USART1_TX: J1.5, U2.29 (PB6)
GND: C1.2, C2.2, C3.1, C4.2, C5.2, C6.2, C7.2, H1.1, H2.1, H3.1, H4.1, J1.3, J2.1, J3.1, J4.1, J5.1, J7.1, J8.1, J9.5 (GND), J9.7 (GND), J9.11 (GNDDetect), J10.1, J11.1, R1.2, R2.1, R3.2, SW1.1, U1.1 (GND), U2.16 (VSS), U2.32 (VSS)
unnamed: D2.1 (K), R3.1

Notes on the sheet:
Ce sont les pins qui s'emboite directetement avec la Raspberry Pi
Passage de l'alimentation des servomoteurs (en 7,4V)
La se trouve les interrupteurs de fin de course. Chaque sorti est un montage pull up
Sorti de chaque commande de rotation et de direction pour chaque stepper
Barrette de pins temporaire qui a permit de position les pins pour shield la raspberry
C'est le module qui permet de connecter le STLINK-V3SET. Une sonde qui permet de programmer le processeur.
7.4V output
BOB_STM32_PCB_ENSEA
ST-Link
Stepper Command Connectors
Power Input
Trous de fixation
1* 100nF per VDD pin
RPI 40 pins connectors Just for footprint
Voltage Regulator

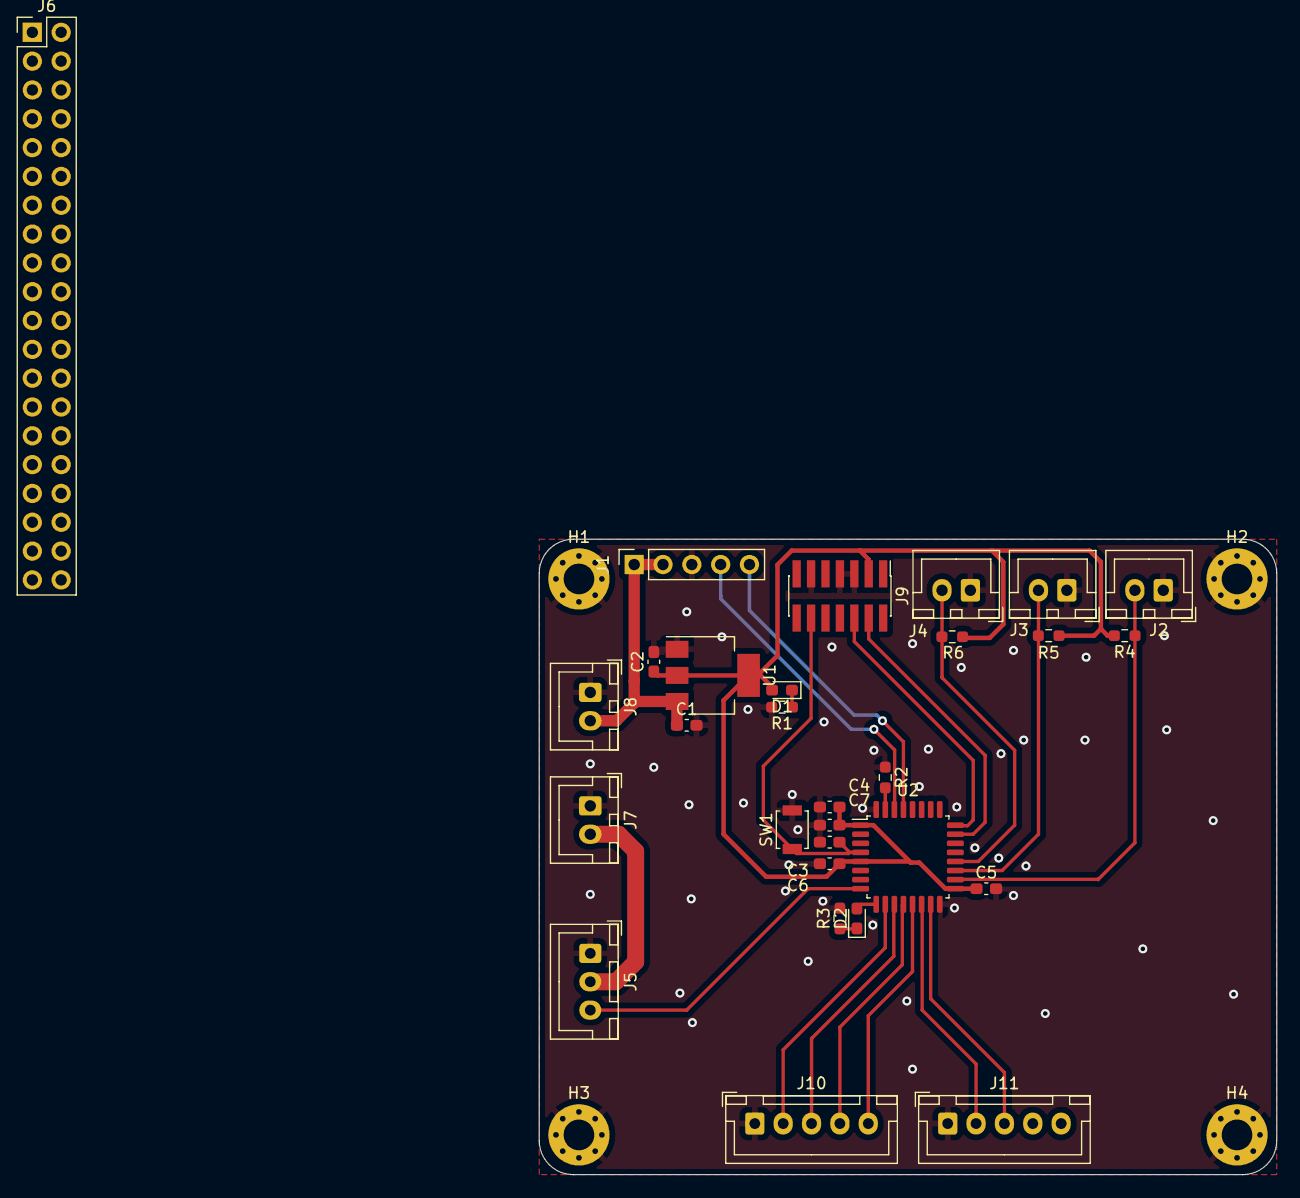
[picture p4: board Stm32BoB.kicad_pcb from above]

Board: 2 copper layers, 65.0 x 56.0 mm, 33 parts (0 on the bottom side), 23 nets.

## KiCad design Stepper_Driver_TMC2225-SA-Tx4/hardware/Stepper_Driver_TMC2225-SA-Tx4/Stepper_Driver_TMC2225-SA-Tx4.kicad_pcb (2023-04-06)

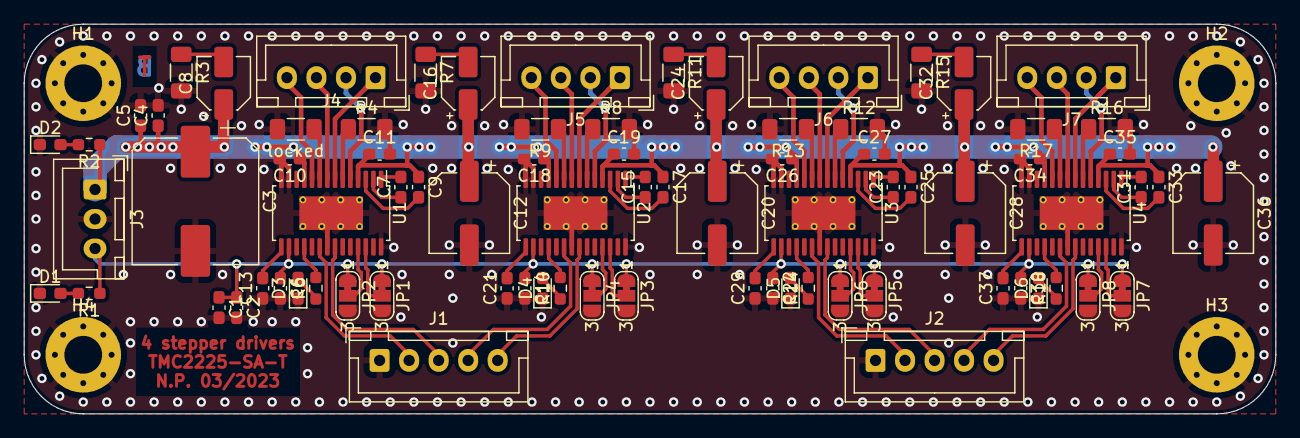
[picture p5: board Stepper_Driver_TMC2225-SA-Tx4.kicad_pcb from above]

Board: 2 copper layers, 106.0 x 33.0 mm, 84 parts (0 on the bottom side), 73 nets.

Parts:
C1, C4: 1uF; C_0603_1608Metric_Pad1.08x0.95mm_HandSolder
C2, C5, C6, C9, C10, C11, C14, C17, C18, C19, C22, C25, C26, C27, C30, C33, C34, C35: 100nF; C_0603_1608Metric_Pad1.08x0.95mm_HandSolder
C3: 100uF; CP_Elec_10x10.5
C7, C15, C23, C31: 22nF; C_0603_1608Metric_Pad1.08x0.95mm_HandSolder
C8, C16, C24, C32: 10uF; CP_Elec_4x5.7
C12, C20, C28, C36: 100uF; CP_Elec_6.3x7.7
C13, C21, C29, C37: 2.2uF; C_0603_1608Metric_Pad1.08x0.95mm_HandSolder
D1, D2, D3, D4, D5, D6: LED; LED_0603_1608Metric_Pad1.05x0.95mm_HandSolder
H1, H2, H3, H4: MountingHole_Pad; MountingHole_3.2mm_M3_Pad_Via
J1, J2: Conn_01x05; JST_XH_B5B-XH-A_1x05_P2.50mm_Vertical
J3: Conn_01x03_Male; JST_XH_B3B-XH-A_1x03_P2.50mm_Vertical
J4, J5, J6, J7: Conn_01x04_Female; JST_XH_B4B-XH-A_1x04_P2.50mm_Vertical
JP1, JP2, JP3, JP4, JP5, JP6, JP7, JP8: SolderJumper_3_Bridged12; SolderJumper-3_P1.3mm_Bridged12_RoundedPad1.0x1.5mm_NumberL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
R1, R2, R6, R10, R14, R18: 1k; R_0603_1608Metric_Pad0.98x0.95mm_HandSolder
R3, R7, R11, R15: 110m; R_1206_3216Metric_Pad1.30x1.75mm_HandSolder
R4, R8, R9, R12, R13, R16, R17: 150m; R_1206_3216Metric_Pad1.30x1.75mm_HandSolder
U1, U2, U3, U4: TMC2225-SA-T; HTSSOP-28-1EP_4.4x9.7mm_P0.65mm_EP2.85x5.4mm_ThermalVias
locked: 150m; R_1206_3216Metric_Pad1.30x1.75mm_HandSolder

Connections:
+3.3V: C1.1, C2.1, C6.1, C14.1, C22.1, C30.1, J3.3, JP1.1 (A), JP2.1 (A), JP3.1 (A), JP4.1 (A), JP5.1 (A), JP6.1 (A), JP7.1 (A), JP8.1 (A), R1.1, U1.16 (VCC_IO), U2.16 (VCC_IO), U3.16 (VCC_IO), U4.16 (VCC_IO)
/TMC2225-1/BRA: R4.1, U1.6 (BRA)
/TMC2225-1/BRB: U1.9 (BRB), locked.1
/TMC2225-1/OA1: J4.1, U1.7 (OA1)
/TMC2225-1/OA2: J4.2, U1.5 (OA2)
/TMC2225-1/OB1: J4.3, U1.8 (OB1)
/TMC2225-1/OB2: J4.4, U1.10 (OB2)
/TMC2225-2/BRA: R8.1, U2.6 (BRA)
/TMC2225-2/BRB: R9.1, U2.9 (BRB)
/TMC2225-2/OA1: J5.1, U2.7 (OA1)
/TMC2225-2/OA2: J5.2, U2.5 (OA2)
/TMC2225-2/OB1: J5.3, U2.8 (OB1)
/TMC2225-2/OB2: J5.4, U2.10 (OB2)
/TMC2225-3/BRA: R12.1, U3.6 (BRA)
/TMC2225-3/BRB: R13.1, U3.9 (BRB)
/TMC2225-3/OA1: J6.1, U3.7 (OA1)
/TMC2225-3/OA2: J6.2, U3.5 (OA2)
/TMC2225-3/OB1: J6.3, U3.8 (OB1)
/TMC2225-3/OB2: J6.4, U3.10 (OB2)
/TMC2225-4/BRA: R16.1, U4.6 (BRA)
/TMC2225-4/BRB: R17.1, U4.9 (BRB)
/TMC2225-4/OA1: J7.1, U4.7 (OA1)
/TMC2225-4/OA2: J7.2, U4.5 (OA2)
/TMC2225-4/OB1: J7.3, U4.8 (OB1)
/TMC2225-4/OB2: J7.4, U4.10 (OB2)
DIR_1: J1.3, U1.22 (STEP)
DIR_2: J1.5, U2.22 (STEP)
DIR_3: J2.3, U3.22 (STEP)
DIR_4: J2.5, U4.22 (STEP)
GND: C1.2, C2.2, C3.2, C4.2, C5.2, C6.2, C10.2, C11.2, C12.2, C13.1, C14.2, C18.2, C19.2, C20.2, C21.1, C22.2, C26.2, C27.2, C28.2, C29.1, C30.2, C34.2, C35.2, C36.2, C37.1, D1.1 (K), D2.1 (K), D3.1 (K), D4.1 (K), D5.1 (K), D6.1 (K), H1.1, H2.1, H3.1, H4.1, J1.1, J2.1, J3.2, JP1.3 (B), JP2.3 (B), JP3.3 (B), JP4.3 (B), JP5.3 (B), JP6.3 (B), JP7.3 (B), JP8.3 (B), R3.2, R4.2, R7.2, R8.2, R9.2, R11.2, R12.2, R13.2, R15.2, R16.2, R17.2, U1.13 (TEST), U1.14 (GND), U1.21 (ENN), U1.28 (GND), U1.29 (PAD), U2.13 (TEST), U2.14 (GND), U2.21 (ENN), U2.28 (GND), U2.29 (PAD), U3.13 (TEST), U3.14 (GND), U3.21 (ENN), U3.28 (GND), U3.29 (PAD), U4.13 (TEST), U4.14 (GND), U4.21 (ENN), U4.28 (GND), U4.29 (PAD), locked.2
unnamed: C7.1, U1.2 (CPI)
unnamed: C7.2, U1.1 (CPO)
unnamed: C8.2, R3.1
unnamed: C9.2, U1.3 (VCP)
unnamed: C13.2, U1.15 (5VOUT)
unnamed: C15.1, U2.2 (CPI)
unnamed: C15.2, U2.1 (CPO)
unnamed: C16.2, R7.1
unnamed: C17.2, U2.3 (VCP)
unnamed: C21.2, U2.15 (5VOUT)
unnamed: C23.1, U3.2 (CPI)
unnamed: C23.2, U3.1 (CPO)
unnamed: C24.2, R11.1
unnamed: C25.2, U3.3 (VCP)
unnamed: C29.2, U3.15 (5VOUT)
unnamed: C31.1, U4.2 (CPI)
unnamed: C31.2, U4.1 (CPO)
unnamed: C32.2, R15.1
unnamed: C33.2, U4.3 (VCP)
unnamed: C37.2, U4.15 (5VOUT)
unnamed: D1.2 (A), R1.2
unnamed: D2.2 (A), R2.2
unnamed: D3.2 (A), R6.1
unnamed: D4.2 (A), R10.1
unnamed: D5.2 (A), R14.1
unnamed: D6.2 (A), R18.1
unnamed: JP1.2 (C), U1.26 (MS2)
unnamed: JP2.2 (C), U1.25 (MS1)
unnamed: JP3.2 (C), U2.26 (MS2)
unnamed: JP4.2 (C), U2.25 (MS1)
unnamed: JP5.2 (C), U3.26 (MS2)
unnamed: JP6.2 (C), U3.25 (MS1)
unnamed: JP7.2 (C), U4.26 (MS2)
unnamed: JP8.2 (C), U4.25 (MS1)
unnamed: R6.2, U1.18 (DIAG)
unnamed: R10.2, U2.18 (DIAG)
unnamed: R14.2, U3.18 (DIAG)
unnamed: R18.2, U4.18 (DIAG)
STEP_1: J1.2, U1.20 (DIR)
STEP_2: J1.4, U2.20 (DIR)
STEP_3: J2.2, U3.20 (DIR)
STEP_4: J2.4, U4.20 (DIR)
VCC: C3.1, C4.1, C5.1, C8.1, C9.1, C10.1, C11.1, C12.1, C16.1, C17.1, C18.1, C19.1, C20.1, C24.1, C25.1, C26.1, C27.1, C28.1, C32.1, C33.1, C34.1, C35.1, C36.1, J3.1, R2.1, U1.4 (VS), U1.11 (VS), U2.4 (VS), U2.11 (VS), U3.4 (VS), U3.11 (VS), U4.4 (VS), U4.11 (VS)
